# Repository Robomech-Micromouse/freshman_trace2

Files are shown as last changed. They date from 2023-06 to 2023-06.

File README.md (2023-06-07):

# freshman_trace2

1,DRCをチェックしておらず、GNDが分離していたので修正しました。

2,フォトリフレクタの配置を裏表逆にしていたので修正しました。

3,羽部分の6ピンを2.00mmピッチにしていたので2.54mmピッチに修正しました。

4,そのほか、外周をGNDで囲んだり、アンテナになっていそうなGNDを極力減らしました。

100mm×100mmに収めているのでJLCPCBで頼むと一週間ぐらいかかる代わりに送料が100円です。ﾔｽｩｲ

pcb

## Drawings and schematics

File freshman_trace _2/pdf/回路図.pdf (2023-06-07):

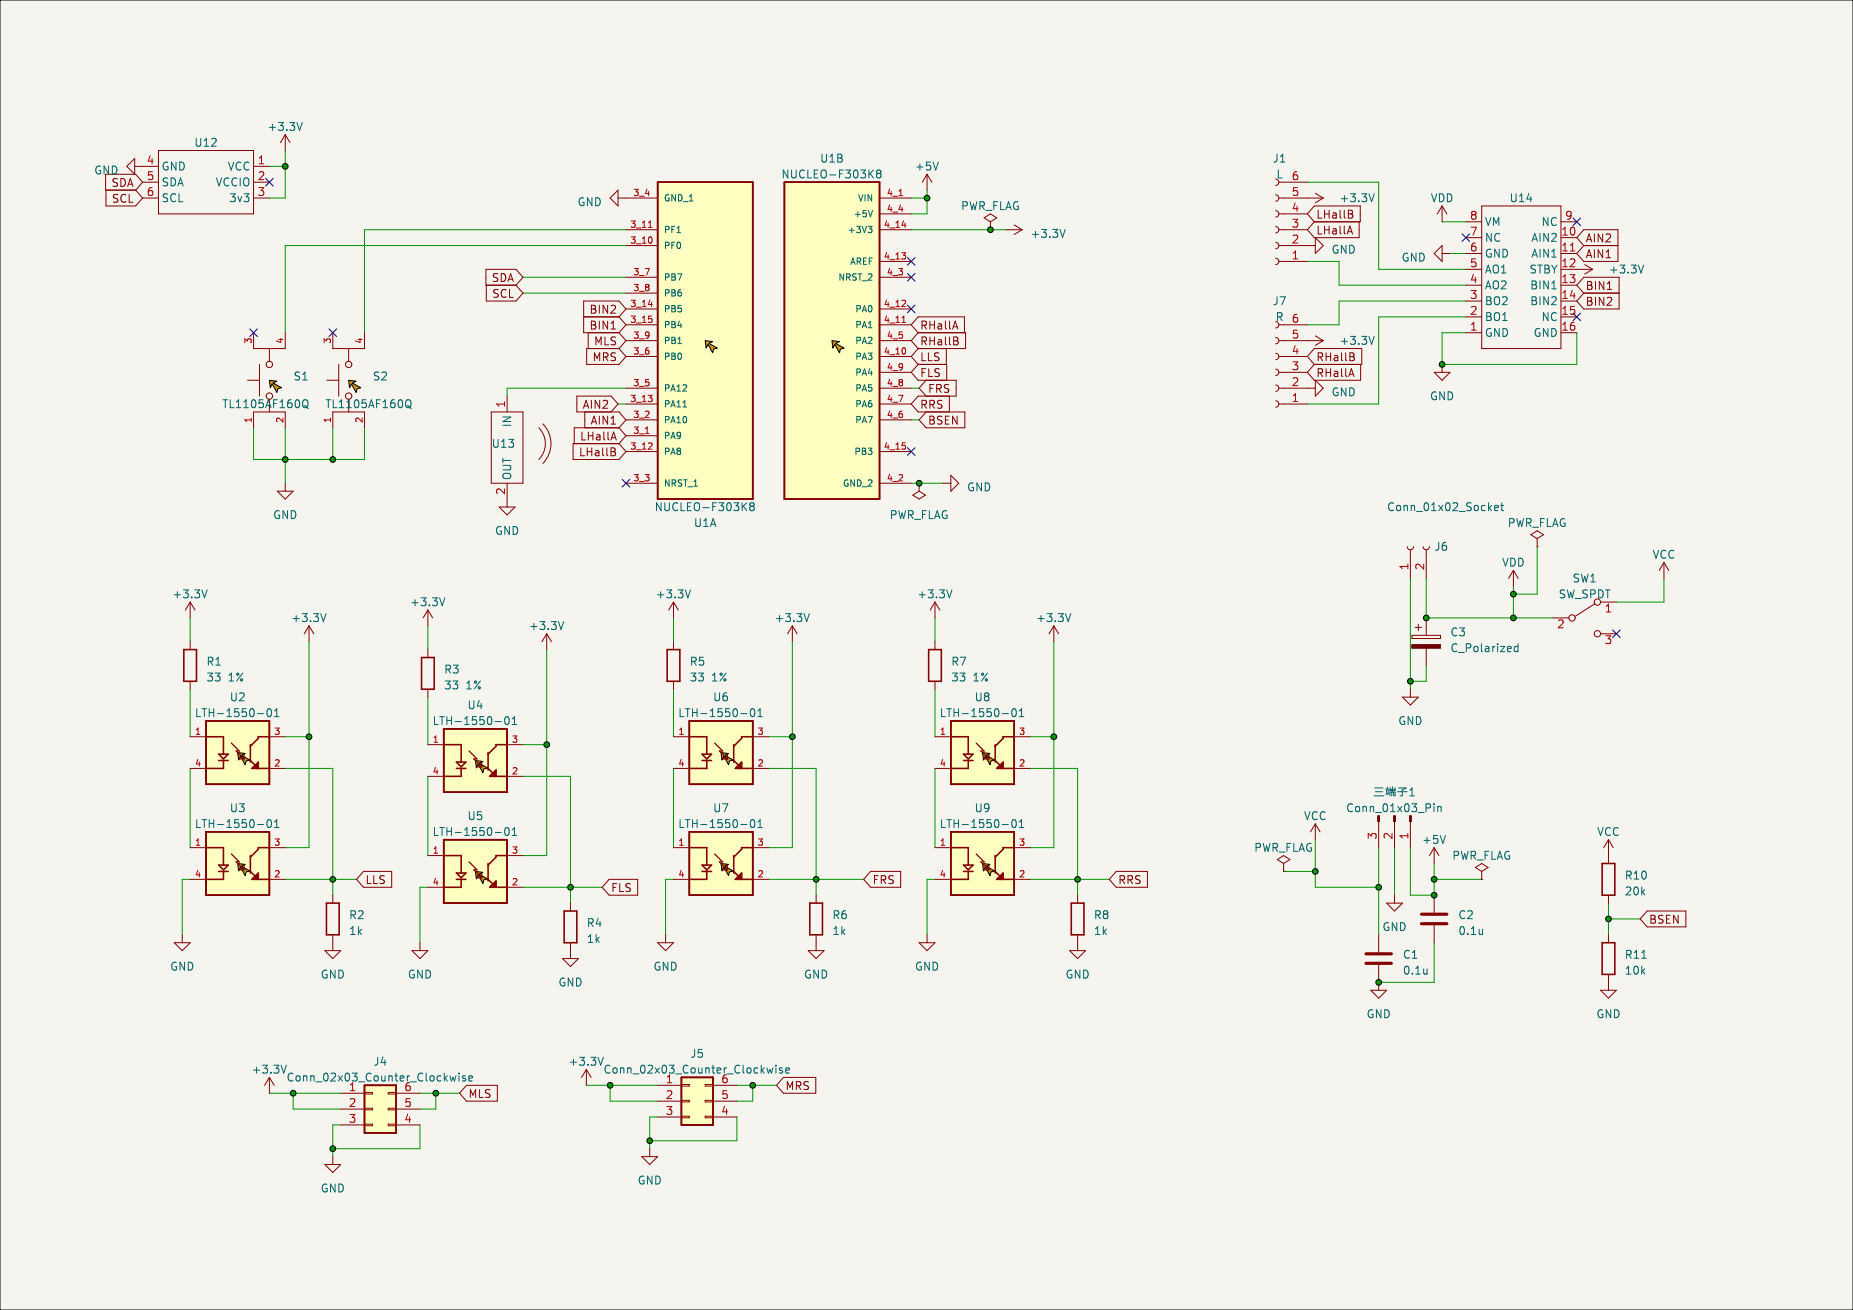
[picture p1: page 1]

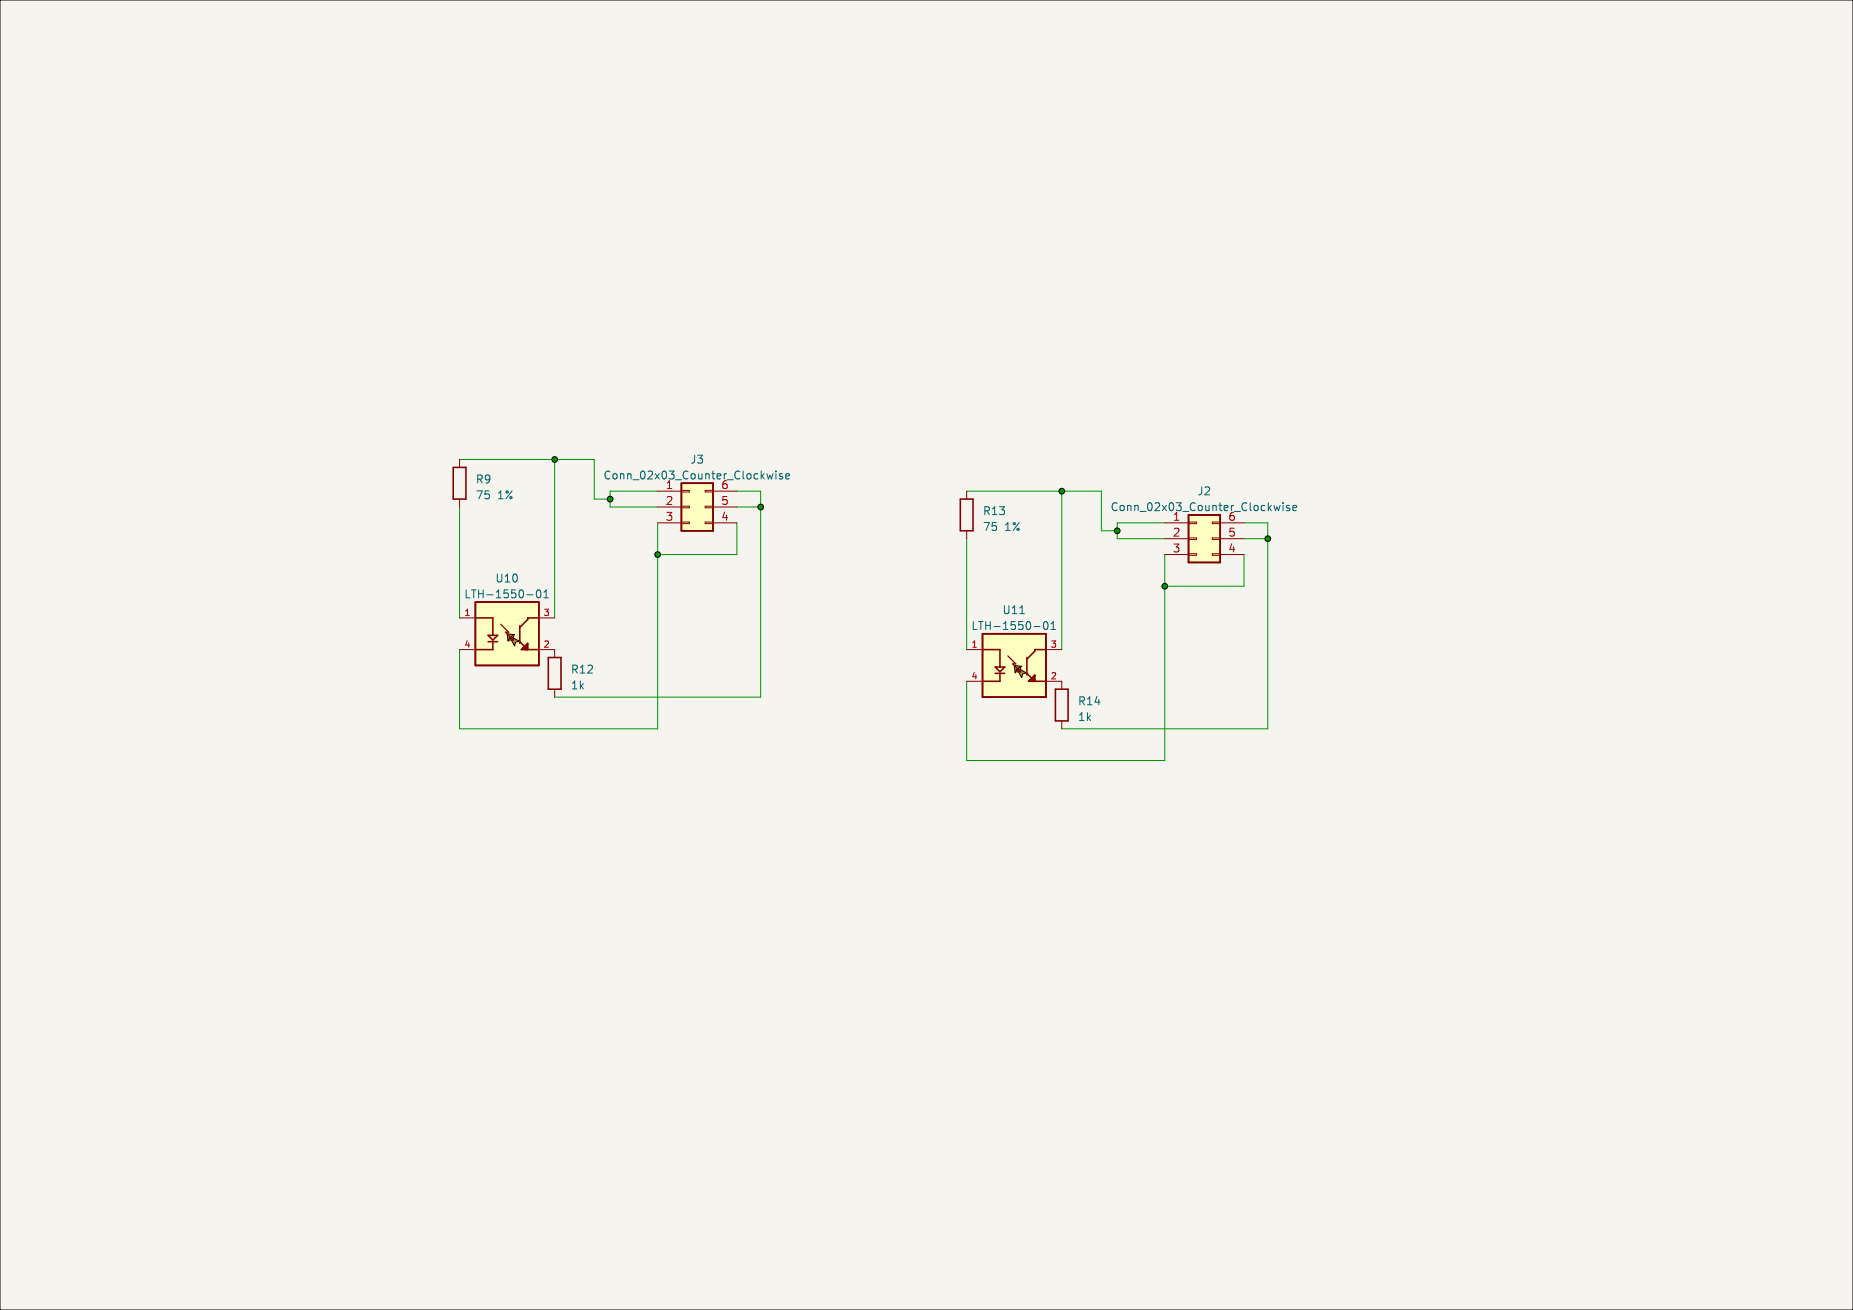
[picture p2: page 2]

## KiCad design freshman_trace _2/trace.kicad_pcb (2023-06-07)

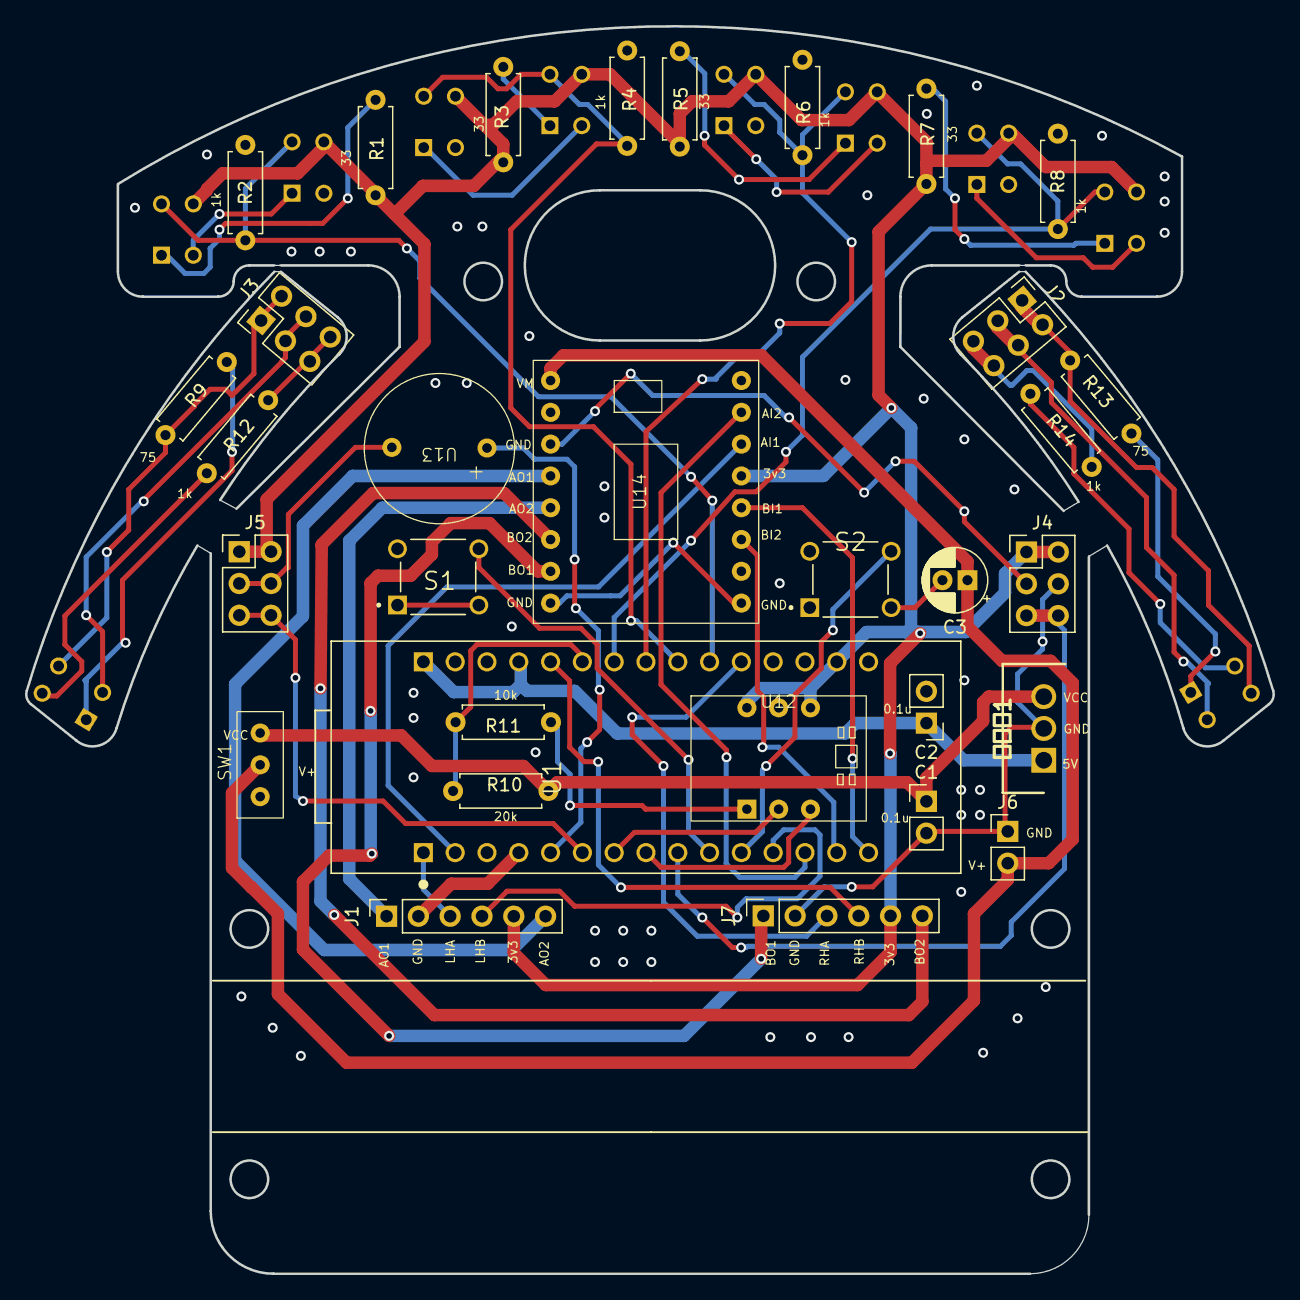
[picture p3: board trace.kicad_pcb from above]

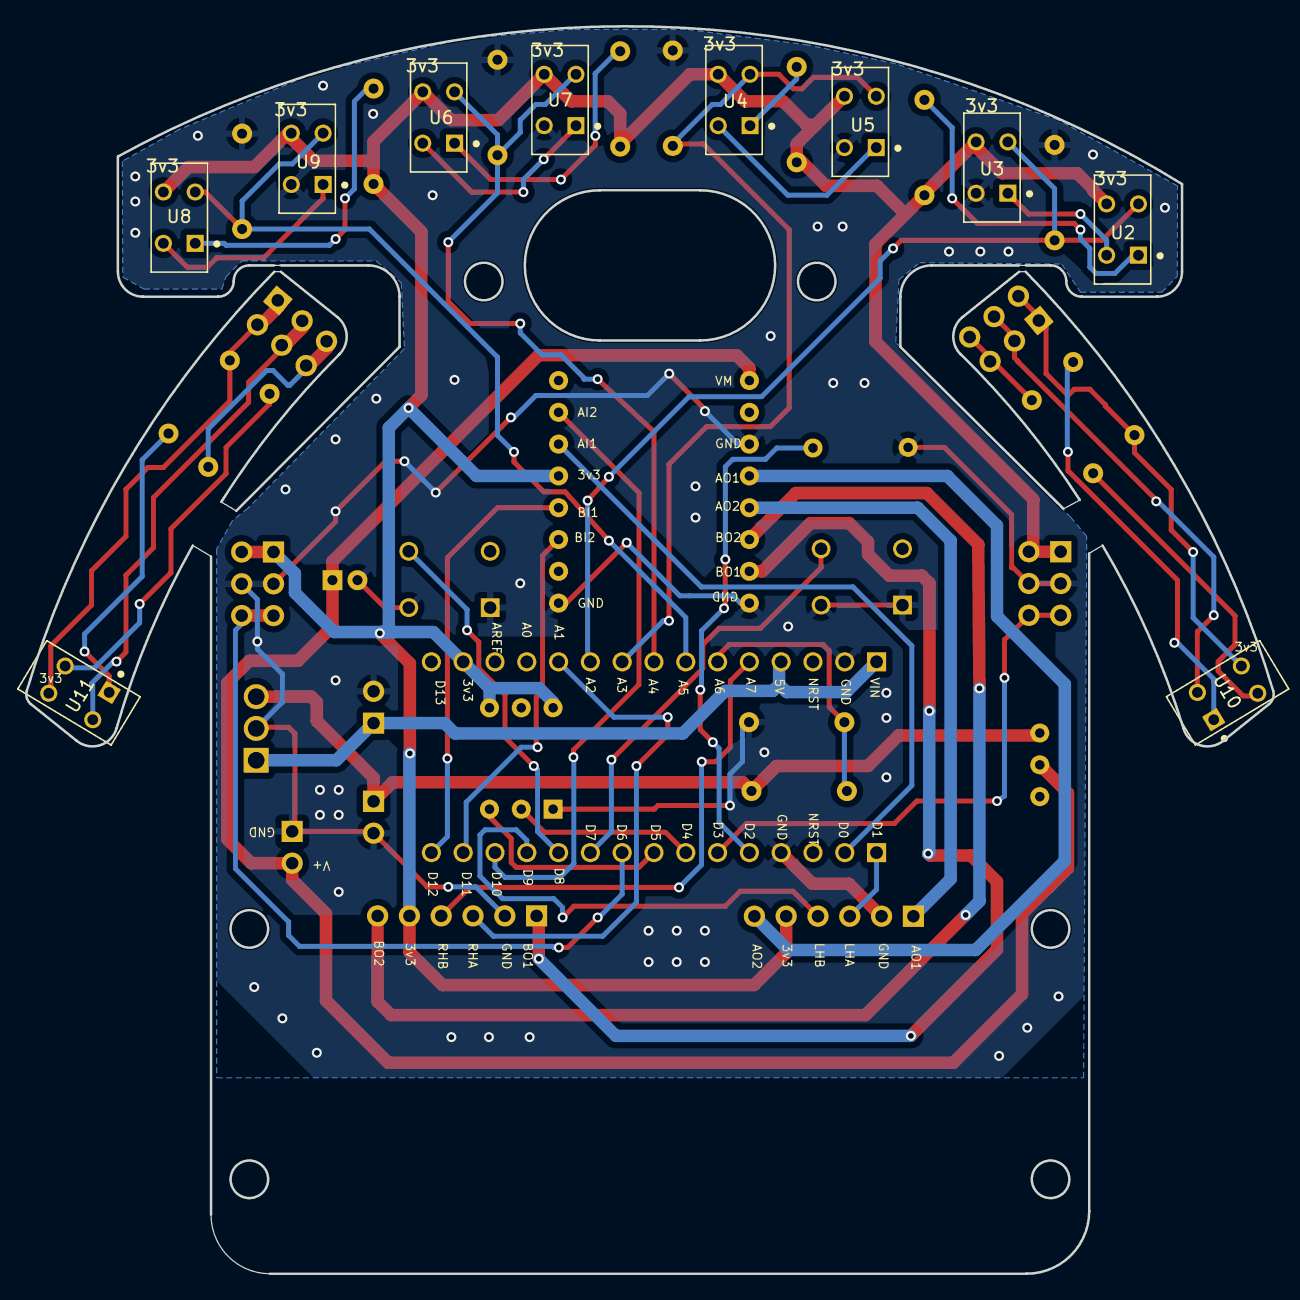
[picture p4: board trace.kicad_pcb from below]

Board: 4 copper layers, 99.6 x 99.6 mm, 42 parts (10 on the bottom side), 47 nets.

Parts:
C1, C2: 0.1u; PinHeader_1x02_P2.54mm_Vertical
C3: C_Polarized; CP_Radial_D5.0mm_P2.00mm
J1: L; PinSocket_1x06_P2.54mm_Vertical
J2, J3, J4, J5: Conn_02x03_Counter_Clockwise; PinHeader_2x03_P2.54mm_Vertical
J6: Conn_01x02_Socket; PinHeader_1x02_P2.54mm_Vertical
J7: R; PinSocket_1x06_P2.54mm_Vertical
R1, R3, R5, R7: 33 1%; R_Axial_DIN0207_L6.3mm_D2.5mm_P7.62mm_Horizontal
R2, R4, R6, R8, R12, R14: 1k; R_Axial_DIN0207_L6.3mm_D2.5mm_P7.62mm_Horizontal
R9, R13: 75 1%; R_Axial_DIN0207_L6.3mm_D2.5mm_P7.62mm_Horizontal
R10: 20k; R_Axial_DIN0207_L6.3mm_D2.5mm_P7.62mm_Horizontal
R11: 10k; R_Axial_DIN0207_L6.3mm_D2.5mm_P7.62mm_Horizontal
S1, S2: TL1105AF160Q; SW_TL1105AF160Q
SW1: SW_SPDT; SS-12D00G3
U1: NUCLEO-F303K8; MODULE_NUCLEO-F303K8
U2, U3, U4, U5, U6, U7, U8, U9, U10, U11: LTH-1550-01; PHOTOINTERRUPTER_LTH-1550-01
U12: BMX055
U13: buzaa
U14: drv8833
三端子1: Conn_01x03_Pin; NJM7805FA

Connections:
+3.3V: J1.5, J4.1, J4.2, J5.1, J5.2, J7.5, R1.1, R3.1, R5.1, R7.1, U1.4_14 (+3V3), U2.3, U3.3, U4.3, U5.3, U6.3, U7.3, U8.3, U9.3, U12.1 (VCC), U12.3 (3v3), U14.12 (STBY)
+5V: C2.1, U1.4_1 (VIN), U1.4_4 (+5V), 三端子1.1
AIN1: U1.3_2 (PA10), U14.11 (AIN1)
AIN2: U1.3_13 (PA11), U14.10 (AIN2)
BIN1: U1.3_15 (PB4), U14.13 (BIN1)
BIN2: U1.3_14 (PB5), U14.14 (BIN2)
BSEN: R10.2, R11.1, U1.4_6 (PA7)
FLS: R4.1, U1.4_9 (PA4), U4.2, U5.2
FRS: R6.1, U1.4_8 (PA5), U6.2, U7.2
GND: C1.2, C2.2, C3.2, J1.2, J4.3, J4.4, J5.3, J5.4, J6.1, J7.2, R2.2, R4.2, R6.2, R8.2, R11.2, S1.1, S1.2, S2.1, S2.2, U1.3_4 (GND_1), U1.4_2 (GND_2), U3.4, U5.4, U7.4, U9.4, U12.4 (GND), U13.2 (OUT), U14.1 (GND), U14.6 (GND), U14.16 (GND), 三端子1.2
LHallA: J1.3, U1.3_1 (PA9)
LHallB: J1.4, U1.3_12 (PA8)
LLS: R2.1, U1.4_10 (PA3), U2.2, U3.2
MLS: J4.5, J4.6, U1.3_9 (PB1)
MRS: J5.5, J5.6, U1.3_6 (PB0)
unnamed: J1.1, U14.4 (AO2)
unnamed: J1.6, U14.5 (AO1)
unnamed: J2.1, J2.2, R13.1, U11.3
unnamed: J2.3, J2.4, U11.4
unnamed: J2.5, J2.6, R14.2
unnamed: J3.1, J3.2, R9.1, U10.3
unnamed: J3.3, J3.4, U10.4
unnamed: J3.5, J3.6, R12.2
unnamed: J7.1, U14.2 (BO1)
unnamed: J7.6, U14.3 (BO2)
unnamed: R1.2, U2.1
unnamed: R3.2, U4.1
unnamed: R5.2, U6.1
unnamed: R7.2, U8.1
unnamed: R9.2, U10.1
unnamed: R12.1, U10.2
unnamed: R13.2, U11.1
unnamed: R14.1, U11.2
unnamed: S1.4, U1.3_10 (PF0)
unnamed: S2.4, U1.3_11 (PF1)
unnamed: U2.4, U3.1
unnamed: U4.4, U5.1
unnamed: U6.4, U7.1
unnamed: U8.4, U9.1
unnamed: U1.3_5 (PA12), U13.1 (IN)
RHallA: J7.3, U1.4_11 (PA1)
RHallB: J7.4, U1.4_5 (PA2)
RRS: R8.1, U1.4_7 (PA6), U8.2, U9.2
SCL: U1.3_8 (PB6), U12.6 (SCL)
SDA: U1.3_7 (PB7), U12.5 (SDA)
VCC: C1.1, R10.1, SW1.1 (A), 三端子1.3
VDD: C3.1, J6.2, SW1.2 (B), U14.8 (VM)
